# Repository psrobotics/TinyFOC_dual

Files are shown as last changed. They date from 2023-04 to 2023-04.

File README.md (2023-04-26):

# TinyFOC_dual

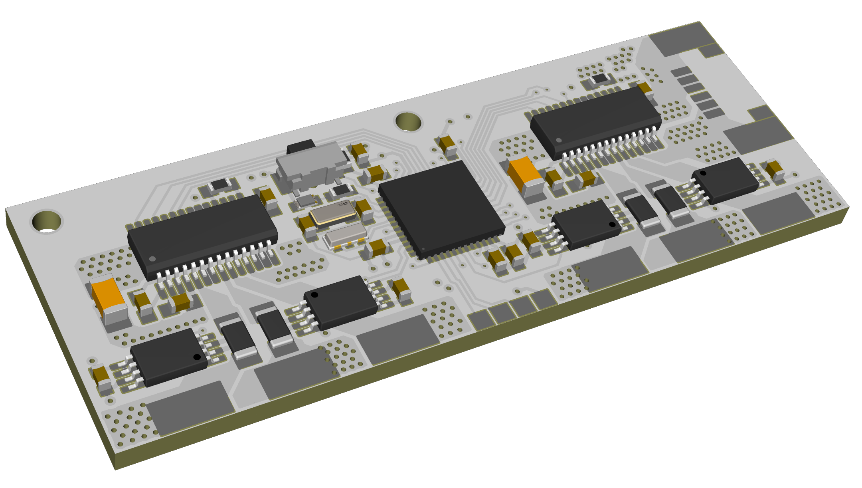
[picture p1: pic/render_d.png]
<br> <br>
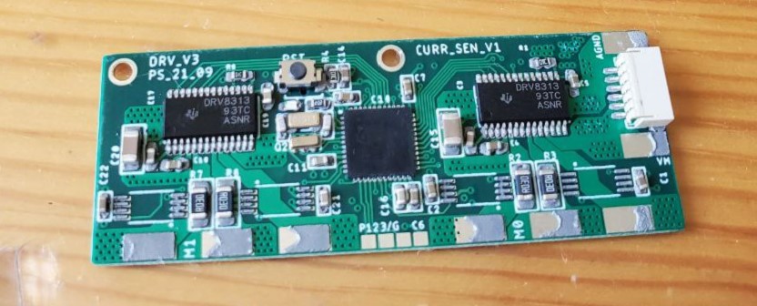
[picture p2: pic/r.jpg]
<br> <br>

* Compact dual channel brushless motor driver with external encoder
* Inline current sensing
* 15 bit GMR-based encoder
* Hardwarer I2C, serial interface
* Input voltage: 9v - 24v, maximum phase current 1.5A
* 4 layer board / FR4 / 1.0mm thickness
* [SimpleFOC](https://github.com/simplefoc) compatible

Design file exported with [Autodesk EAGLE](https://www.autodesk.com/products/eagle/overview?term=1-YEAR&tab=subscription)

## ICs
* MCU [STM32F401CCU6](https://www.st.com/en/microcontrollers-microprocessors/stm32f401cc.html)
* Motor driver [DRV8313](https://www.ti.com/product/DRV8313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) or [MS8313](https://www.lcsc.com/product-detail/Others_Hangzhou-Ruimeng-Tech-MS8313_C231942.html)
* Current sensing AMP [INA240A2PWR](https://www.ti.com/product/INA240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)
* Encoder [TLE 5012B E1000](https://www.infineon.com/cms/en/product/sensor/magnetic-sensors/magnetic-position-sensors/angle-sensors/tle5012b-e1000/)

## Pin Out
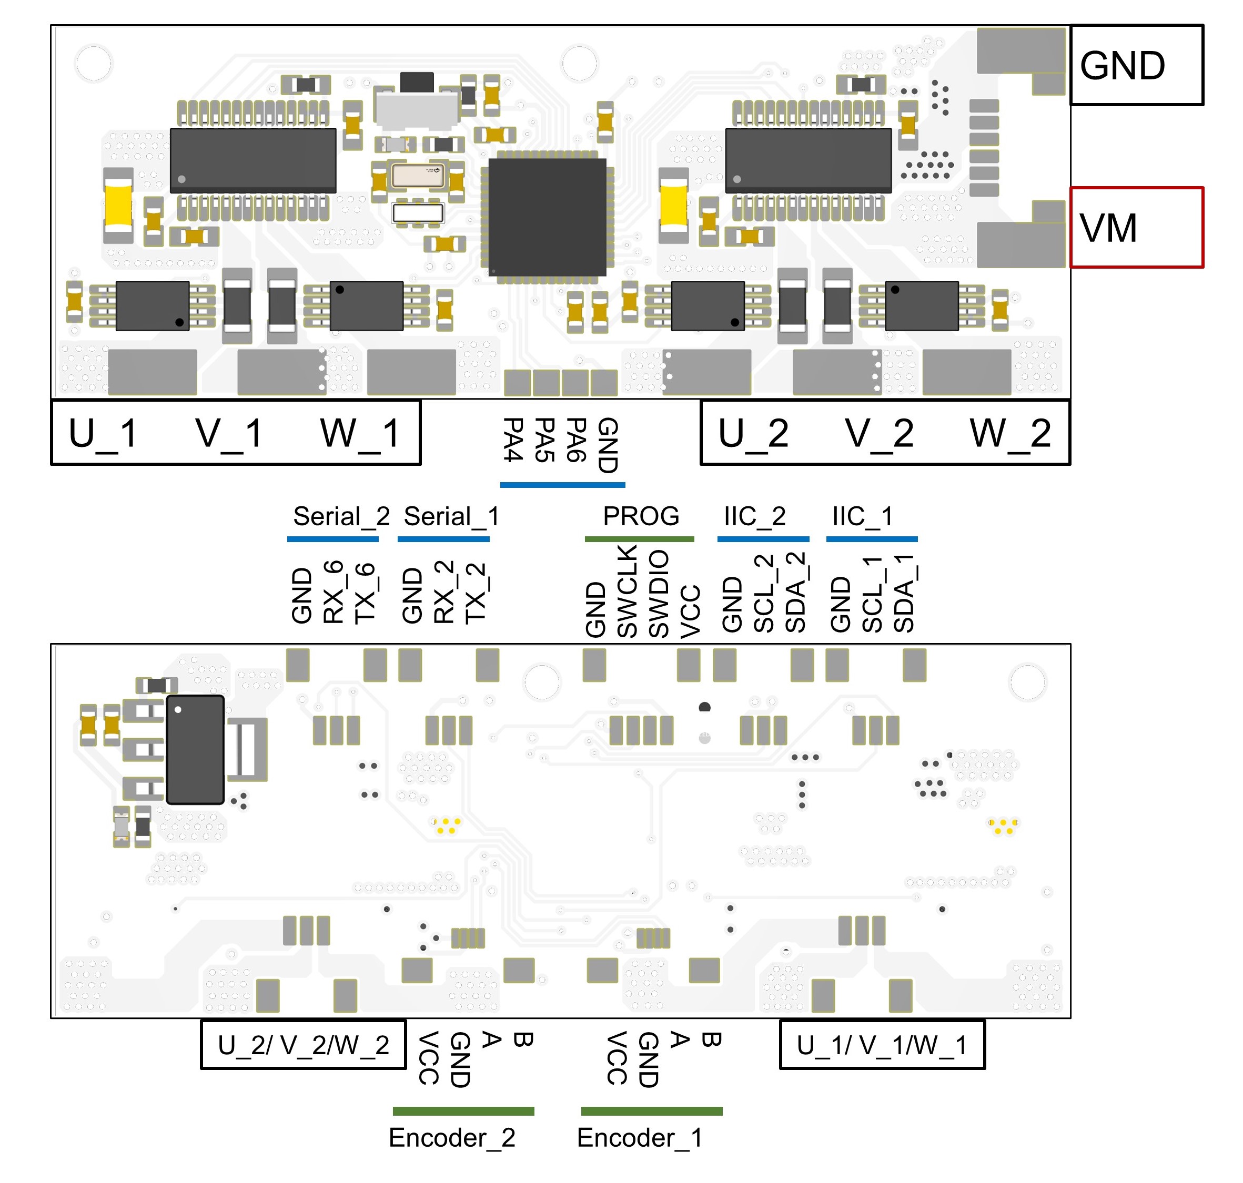
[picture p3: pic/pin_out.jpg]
<br> <br>

## License
MIT License

## Contact
* Shuang Peng, {shuangpe}@usc.edu

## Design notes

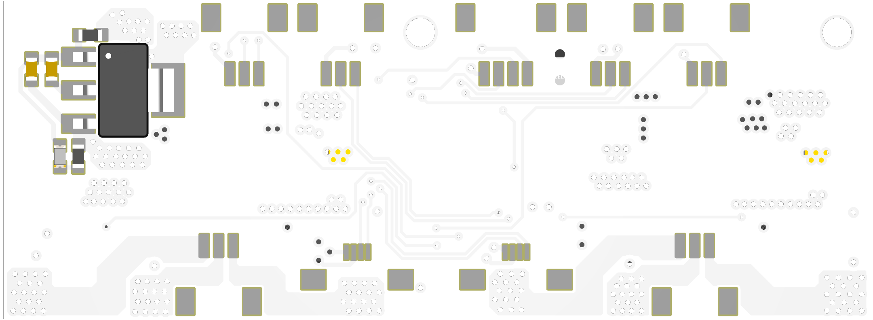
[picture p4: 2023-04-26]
pic/render_b.png

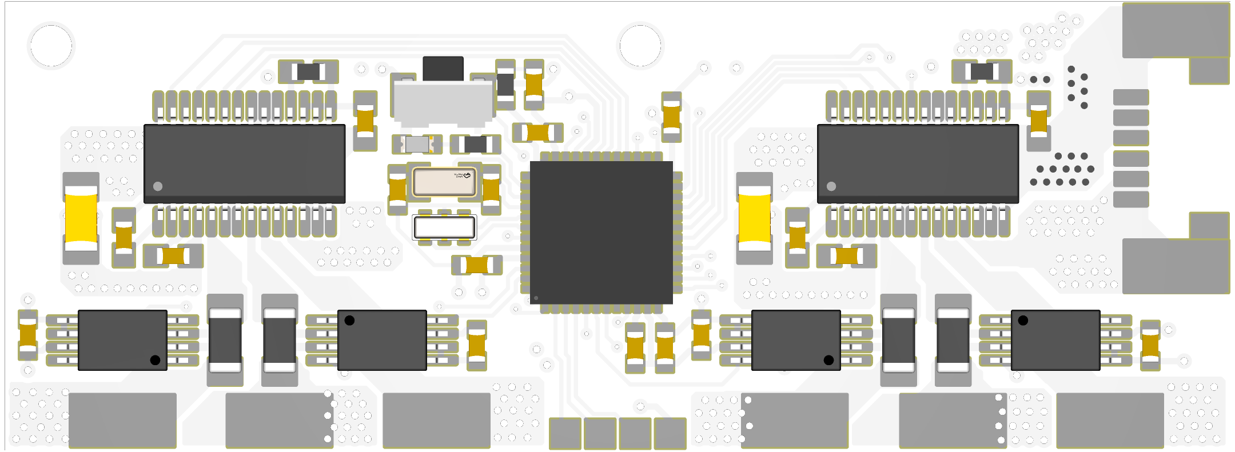
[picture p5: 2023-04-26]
pic/render_t.png

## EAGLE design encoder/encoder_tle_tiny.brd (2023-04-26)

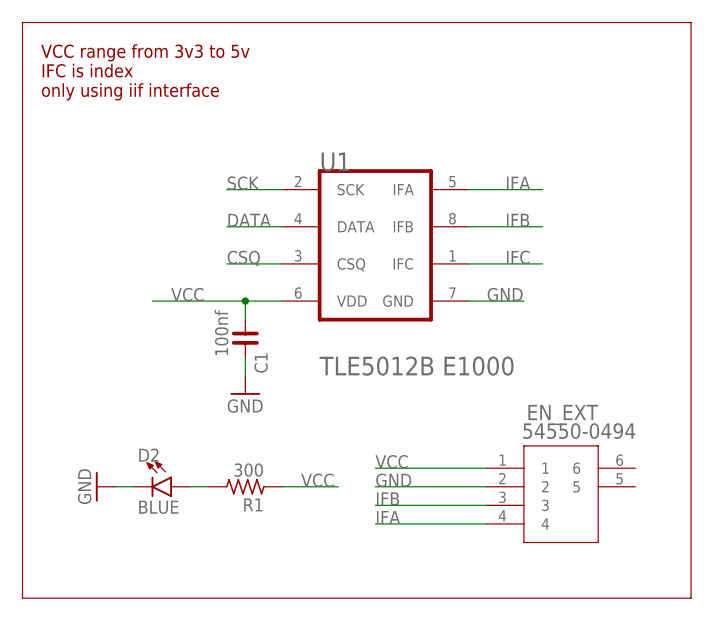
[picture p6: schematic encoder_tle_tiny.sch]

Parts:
C1: 100nf; C0603
D2: BLUE; LED-0603
EN_EXT: 54550-0494; CON4_1X4_DRB2_MOL
R1: 300; R0603
U1: INFINEON_TLE5012B_E1000INFINEON_TLE5012B_E1000_0_1; INFINEON_TLE5012B_E1000_1

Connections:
CSQ: U1.3 (CSQ)
DATA: U1.4 (DATA)
GND: C1.2, D2.C, EN_EXT.2, U1.7 (GND)
IFA: EN_EXT.4, U1.5 (IFA)
IFB: EN_EXT.3, U1.8 (IFB)
IFC: U1.1 (IFC)
unnamed: D2.A, R1.2
SCK: U1.2 (SCK)
VCC: C1.1, EN_EXT.1, R1.1, U1.6 (VDD)

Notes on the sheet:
VCC range from 3v3 to 5v IFC is index only using iif interface

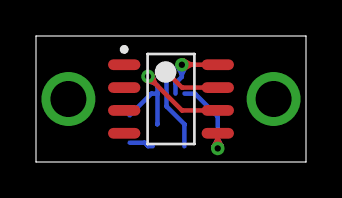
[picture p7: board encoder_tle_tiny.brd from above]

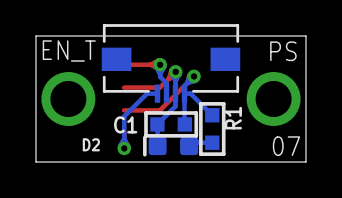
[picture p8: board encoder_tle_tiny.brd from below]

Board: 2 copper layers, 15.0 x 7.0 mm, 5 parts (4 on the bottom side), 5 nets.

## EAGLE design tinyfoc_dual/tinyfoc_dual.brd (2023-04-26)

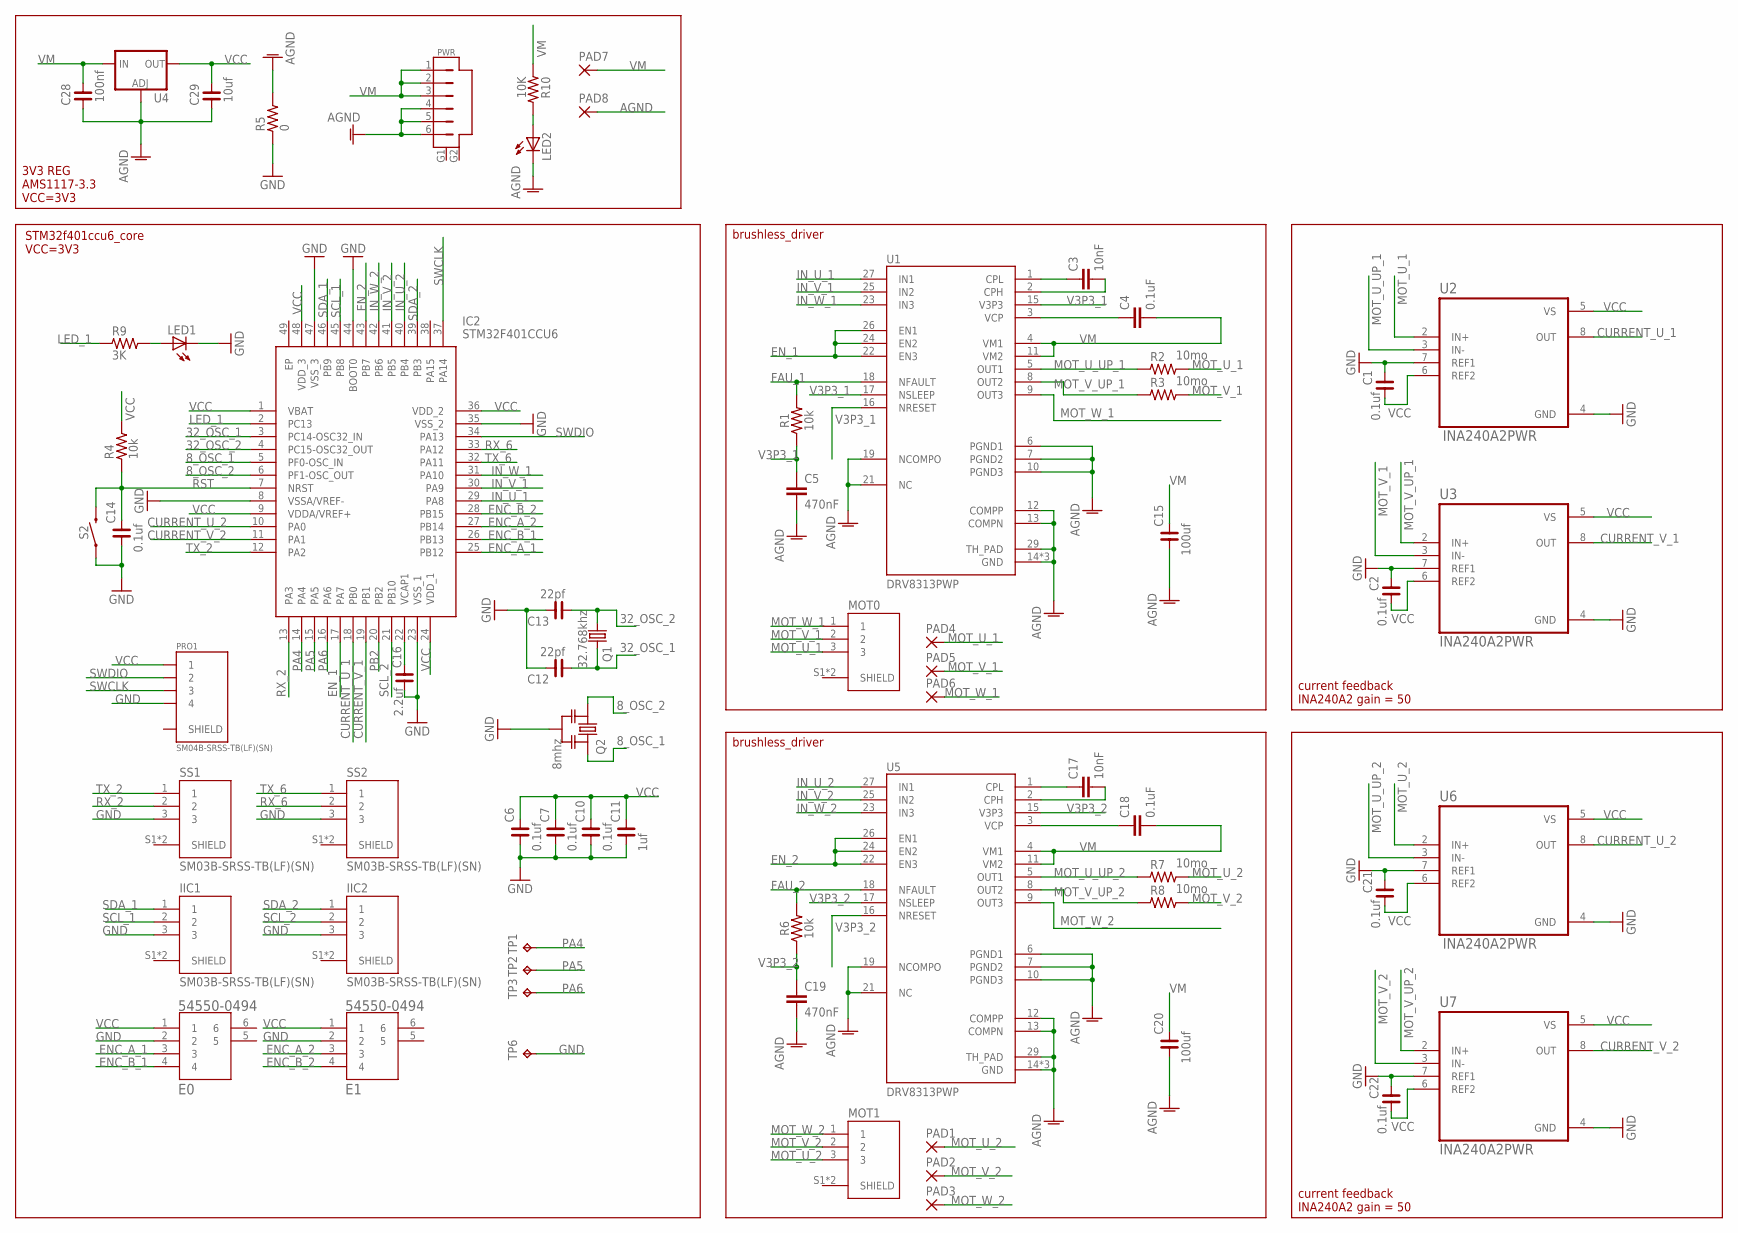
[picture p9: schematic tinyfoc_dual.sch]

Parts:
C1, C2, C6, C7, C10, C14, C21, C22: 0.1uf; C0603
C3, C17: 10nF; 0603
C4, C18: 0.1uF; 0603
C5, C19: 470nF; 0603
C11: 1uf; C0603
C12, C13: 22pf; C0603
C15, C20: 100uf; C1206
C16: 2.2uf; C0603
C28: 100nf; C0603
C29: 10uf; C0603
E0, E1: 54550-0494; CON4_1X4_DRB2_MOL
IC2: STM32F401CCU6; QFN50P700X700X60-49N
IIC1, IIC2: SM03B-SRSS-TB(LF)(SN); JST_SM03B-SRSS-TB(LF)(SN)
LED1, LED2: LEDCHIPLED_0603; CHIPLED_0603
MOT0, MOT1: SM03B-SRSS-TB(LF)(SN); JST_SM03B-SRSS-TB(LF)(SN)
PAD1, PAD2, PAD3, PAD4, PAD5, PAD6, PAD7, PAD8: SMD5; SMD2,54-5,08
PRO1: SM04B-SRSS-TB(LF)(SN); JST_SM04B-SRSS-TB(LF)(SN)
PWR: SM06B-SRSS-TB; SM06B
Q1: 32.768khz; 3.2X1.5
Q2: 8mhz; RESONATOR_MURATA2
R1, R6: 10k; 0603
R2, R3, R7, R8: 10mo; R1206
R4: 10k; R0603
R5: 0; R0603
R9: 3K; R0603
R10: 10K; R0603
S2: MOMENTARY-SWITCH-SPST-SMD-RIGHT-ANGLE; TACTILE_SWITCH_SMD_RIGHT_ANGLE
SS1, SS2: SM03B-SRSS-TB(LF)(SN); JST_SM03B-SRSS-TB(LF)(SN)
TP1, TP2, TP3, TP6: TPTP14SQ; TP14SQ
U1, U5: DRV8313PWP; SOP28P65_970X640X120L60X24T483X275N
U2, U3, U6, U7: INA240A2PWR; SOP65P640X120-8N
U4: V_REG_LM1117SOT223; SOT223

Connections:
8_OSC_1: IC2.5 (PF0-OSC_IN), Q2.3
8_OSC_2: IC2.6 (PF1-OSC_OUT), Q2.1
32_OSC_1: C12.1, IC2.3 (PC14-OSC32_IN), Q1.2
32_OSC_2: C13.1, IC2.4 (PC15-OSC32_OUT), Q1.1
AGND: C5.2, C15.1, C19.2, C20.1, C28.1, C29.1, LED2.C, PAD8.1, PWR.4, PWR.5, PWR.6, R5.2, U1.6 (PGND1), U1.7 (PGND2), U1.10 (PGND3), U1.12 (COMPP), U1.13 (COMPN), U1.14 (GND), U1.19 (NCOMPO), U1.20 (GND), U1.21 (NC), U1.28 (GND), U1.29 (TH_PAD), U4.1 (ADJ), U5.6 (PGND1), U5.7 (PGND2), U5.10 (PGND3), U5.12 (COMPP), U5.13 (COMPN), U5.14 (GND), U5.19 (NCOMPO), U5.20 (GND), U5.21 (NC), U5.28 (GND), U5.29 (TH_PAD)
CURRENT_U_1: IC2.18 (PB0), U2.8 (OUT)
CURRENT_U_2: IC2.10 (PA0), U6.8 (OUT)
CURRENT_V_1: IC2.19 (PB1), U3.8 (OUT)
CURRENT_V_2: IC2.11 (PA1), U7.8 (OUT)
ENC_A_1: E0.3, IC2.25 (PB12)
ENC_A_2: E1.3, IC2.27 (PB14)
ENC_B_1: E0.4, IC2.26 (PB13)
ENC_B_2: E1.4, IC2.28 (PB15)
EN_1: IC2.17 (PA7), U1.22 (EN3), U1.24 (EN2), U1.26 (EN1)
EN_2: IC2.43 (PB7), U5.22 (EN3), U5.24 (EN2), U5.26 (EN1)
FAU_1: R1.2, U1.18 (NFAULT)
FAU_2: R6.2, U5.18 (NFAULT)
GND: C1.2, C2.2, C6.1, C7.1, C10.1, C11.1, C12.2, C13.2, C14.1, C16.1, C21.2, C22.2, E0.2, E1.2, IC2.8 (VSSA/VREF-), IC2.23 (VSS_1), IC2.35 (VSS_2), IC2.44 (BOOT0), IC2.47 (VSS_3), IIC1.3, IIC2.3, LED1.C, PRO1.4, Q2.2, R5.1, S2.1, SS1.3, SS2.3, TP6.TP, U2.4 (GND), U2.7 (REF1), U3.4 (GND), U3.7 (REF1), U6.4 (GND), U6.7 (REF1), U7.4 (GND), U7.7 (REF1)
IN_U_1: IC2.29 (PA8), U1.27 (IN1)
IN_U_2: IC2.40 (PB4), U5.27 (IN1)
IN_V_1: IC2.30 (PA9), U1.25 (IN2)
IN_V_2: IC2.41 (PB5), U5.25 (IN2)
IN_W_1: IC2.31 (PA10), U1.23 (IN3)
IN_W_2: IC2.42 (PB6), U5.23 (IN3)
LED_1: IC2.2 (PC13), R9.1
MOT_U_1: MOT0.3, PAD4.1, R2.2, U2.2 (IN+)
MOT_U_2: MOT1.3, PAD1.1, R7.2, U6.2 (IN+)
MOT_U_UP_1: R2.1, U1.5 (OUT1), U2.3 (IN-)
MOT_U_UP_2: R7.1, U5.5 (OUT1), U6.3 (IN-)
MOT_V_1: MOT0.2, PAD5.1, R3.2, U3.3 (IN-)
MOT_V_2: MOT1.2, PAD2.1, R8.2, U7.3 (IN-)
MOT_V_UP_1: R3.1, U1.8 (OUT2), U3.2 (IN+)
MOT_V_UP_2: R8.1, U5.8 (OUT2), U7.2 (IN+)
MOT_W_1: MOT0.1, PAD6.1, U1.9 (OUT3)
MOT_W_2: MOT1.1, PAD3.1, U5.9 (OUT3)
unnamed: C16.2, IC2.22 (VCAP1)
unnamed: C17.1, U5.1 (CPL)
unnamed: C3.1, U1.1 (CPL)
unnamed: C3.2, U1.2 (CPH)
unnamed: C4.1, U1.3 (VCP)
unnamed: LED2.A, R10.2
unnamed: C17.2, U5.2 (CPH)
unnamed: C18.1, U5.3 (VCP)
unnamed: LED1.A, R9.2
PA4: IC2.14 (PA4), TP1.TP
PA5: IC2.15 (PA5), TP2.TP
PA6: IC2.16 (PA6), TP3.TP
PB2: IC2.20 (PB2)
RST: C14.2, IC2.7 (NRST), R4.1, S2.2
RX_2: IC2.13 (PA3), SS1.2
RX_6: IC2.33 (PA12), SS2.2
SCL_1: IC2.45 (PB8), IIC1.2
SCL_2: IC2.21 (PB10), IIC2.2
SDA_1: IC2.46 (PB9), IIC1.1
SDA_2: IC2.39 (PB3), IIC2.1
SWCLK: IC2.37 (PA14), PRO1.3
SWDIO: IC2.34 (PA13), PRO1.2
TX_2: IC2.12 (PA2), SS1.1
TX_6: IC2.32 (PA11), SS2.1
V3P3_1: C5.1, R1.1, U1.15 (V3P3), U1.16 (NRESET), U1.17 (NSLEEP)
V3P3_2: C19.1, R6.1, U5.15 (V3P3), U5.16 (NRESET), U5.17 (NSLEEP)
VCC: C1.1, C2.1, C6.2, C7.2, C10.2, C11.2, C21.1, C22.1, C29.2, E0.1, E1.1, IC2.1 (VBAT), IC2.9 (VDDA/VREF+), IC2.24 (VDD_1), IC2.36 (VDD_2), IC2.48 (VDD_3), PRO1.1, R4.2, U2.5 (VS), U2.6 (REF2), U3.5 (VS), U3.6 (REF2), U4.2 (OUT), U4.4 (OUT), U6.5 (VS), U6.6 (REF2), U7.5 (VS), U7.6 (REF2)
VM: C4.2, C15.2, C18.2, C20.2, C28.2, PAD7.1, PWR.1, PWR.2, PWR.3, R10.1, U1.4 (VM1), U1.11 (VM2), U4.3 (IN), U5.4 (VM1), U5.11 (VM2)

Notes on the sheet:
brushless_driver
current feedback INA240A2 gain = 50
STM32f401ccu6_core VCC=3V3
3V3 REG AMS1117-3.3 VCC=3V3

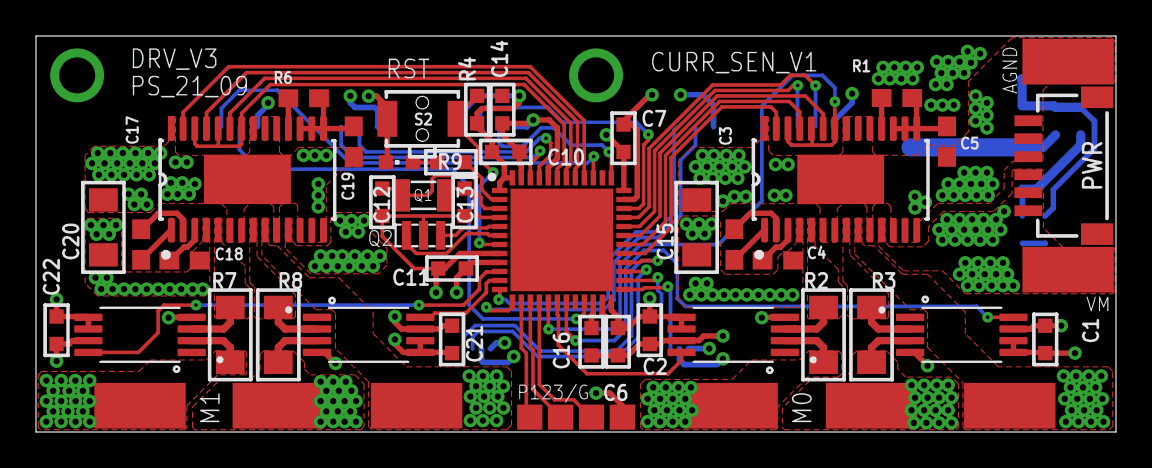
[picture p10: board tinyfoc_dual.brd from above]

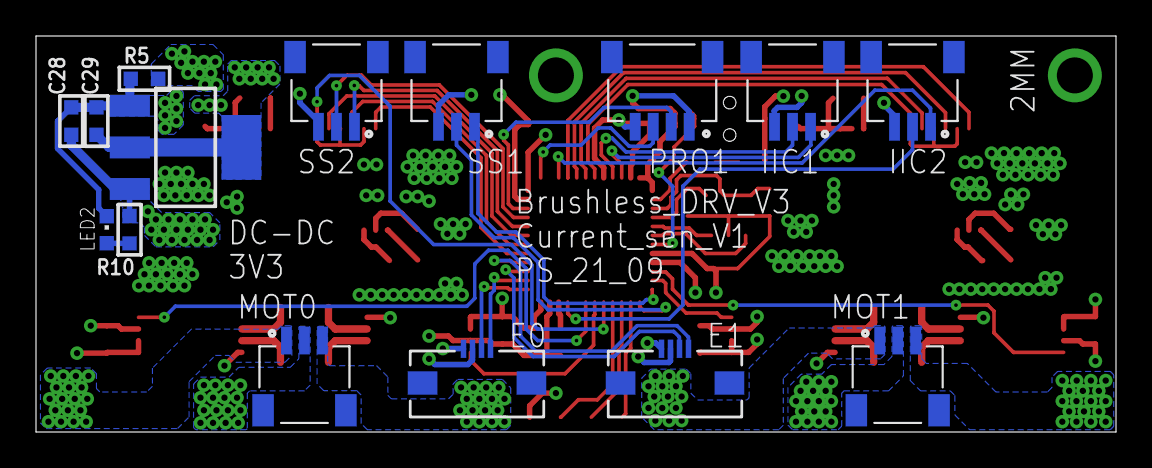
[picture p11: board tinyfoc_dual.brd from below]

Board: 4 copper layers, 60.0 x 22.0 mm, 67 parts (15 on the bottom side), 62 nets.

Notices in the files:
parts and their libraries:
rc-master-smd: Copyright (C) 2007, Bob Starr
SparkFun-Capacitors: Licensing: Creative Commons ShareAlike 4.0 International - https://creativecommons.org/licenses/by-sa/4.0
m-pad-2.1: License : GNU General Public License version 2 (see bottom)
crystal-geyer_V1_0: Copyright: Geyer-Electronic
